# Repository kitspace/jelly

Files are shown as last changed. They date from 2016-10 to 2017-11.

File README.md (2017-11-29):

# Light-following Jellyfish Bristlebot

This is a small light following robot that consists of a simple analog circuit and uses pager vibration motors and toothbrush heads as a form of locomotion. 
This was heavily inspired by [Facelesstech's project](https://facelesstech.wordpress.com/2016/08/15/light-following-bristle-bot/) but adds jellyfishness (with the help of [svg2mod](https://github.com/mtl/svg2mod)).

## Parts
You can buy most of the parts through the [Kitspace page](https://kitspace.org/jelly) but you will also need:

- 2 toothbrush heads (use some old ones!)
- A LiPo battery with a JST connector and built-in protection, anything between 200 - 400mAh should work well (e.g. [from Adafruit](https://www.adafruit.com/product/2750))
- 2 pager vibration motors (e.g. [from Amazon](https://www.amazon.co.uk/Vibration-Motor-TOOGOO-4-6mm-2000RPM/dp/B01H01PXQ2))
- 3 100mm cable ties (e.g. [from Amazon](https://www.amazon.co.uk/Sealey-CT25101-Cable-Ties-100mm/dp/B000RO146I))

## Instructions

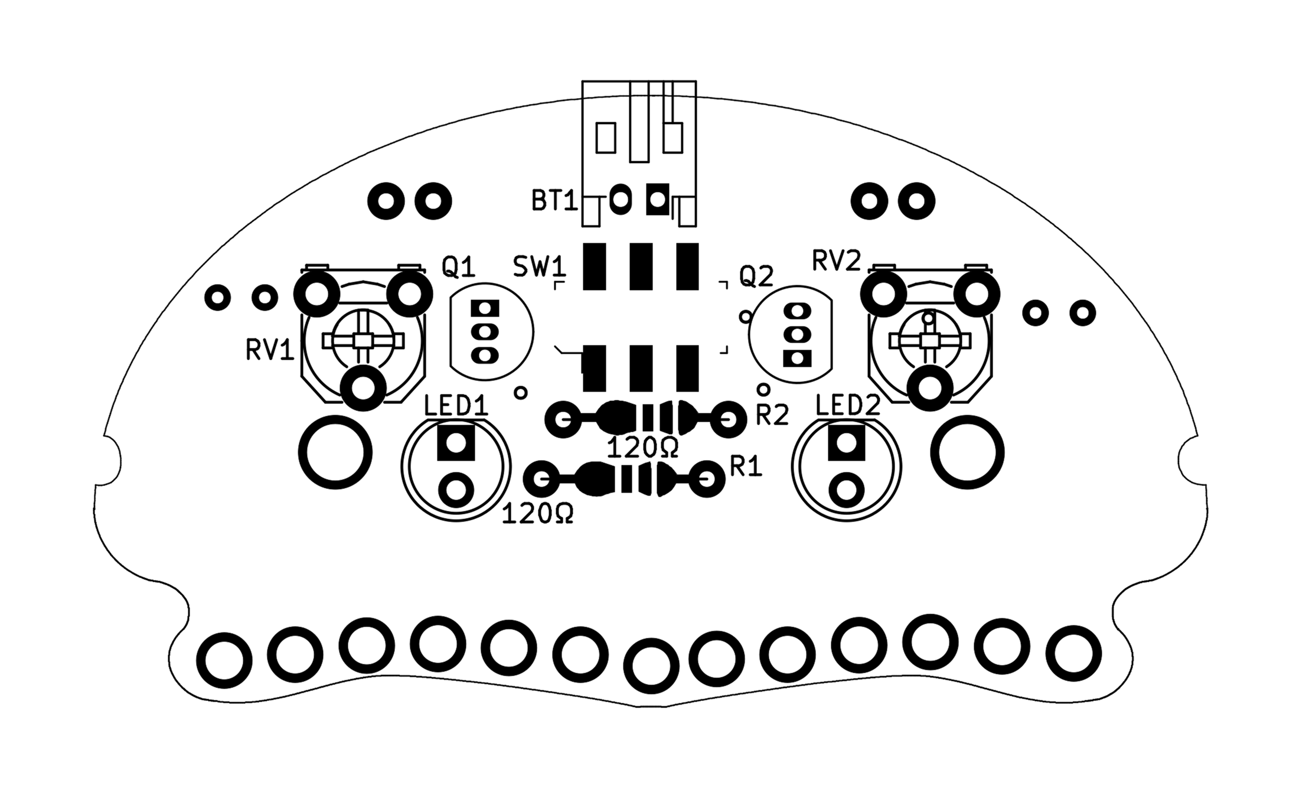
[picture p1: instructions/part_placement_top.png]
top part placement image

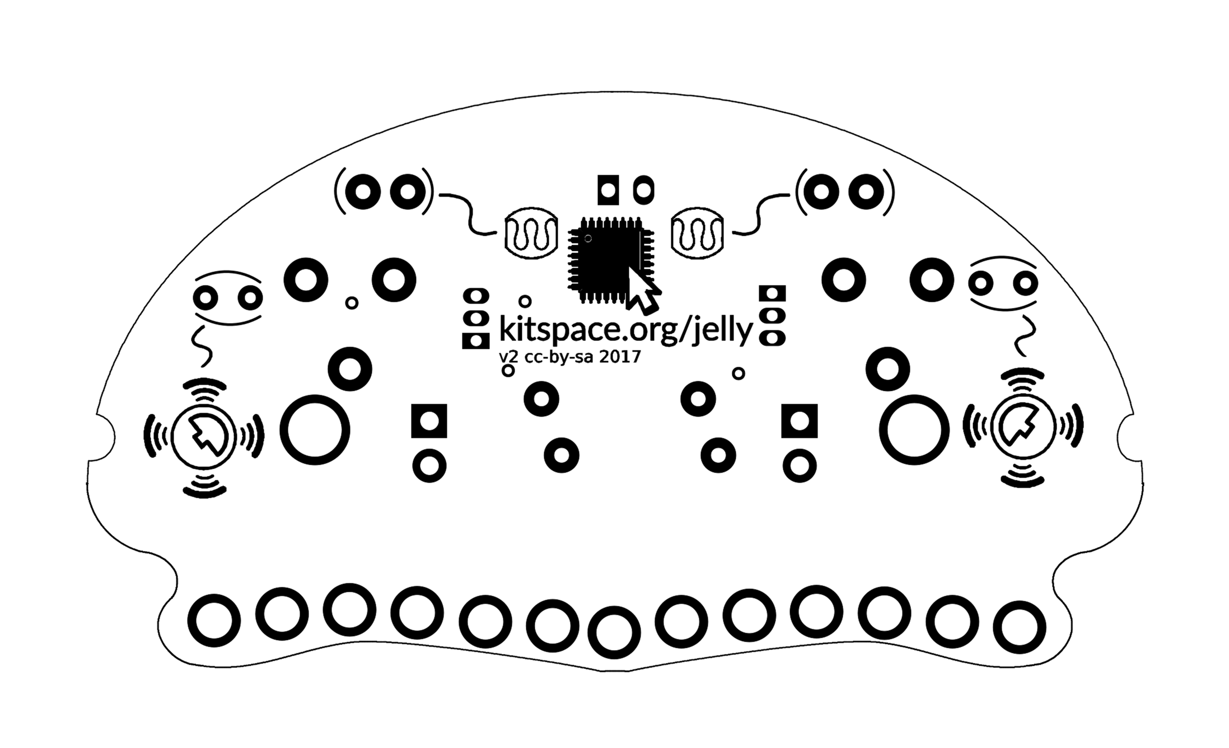
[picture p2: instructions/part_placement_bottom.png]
bottom part placement image


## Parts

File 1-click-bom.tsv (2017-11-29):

References | Qty | Description | Manufacturer | MPN | Digikey | Mouser | RS | Newark | Farnell
BT1 | 1 | Battery connector | JST | S2B-PH-K-S(LF)(SN) | 455-1719-ND |  | 6881353P | 38K8066 | 9491902
LED1, LED2 | 2 | 5MM LED Red | Vishay | TLHK5100 | 751-1118-ND | 78TLHK5100 | 8187580 | 33C1301 | 1328315
PHOTO1, PHOTO2 | 2 | Light dependant resistor |  |  | NSL-19M51-ND |  | 9146710 | 14J5050 | 3168335
Q1, Q2 | 2 | N-Channel MOSFET Tranistor | ON Semiconductor | 2N7000 | 2N7000FS-ND | 5122N7000 | 6714733 | 98K6267 | 9845178
R1, R2 | 2 | Resistor through-hole 1k | TE Connectivity | LR1F1K0 | A105951CT-ND | 594MBB02070C1001FC1 | 148506 | 95W7808 | 2614370
RV1, RV2 | 2 | Trimpot | Bourns | 3306F-1-203 | 3306F-203-ND | 6523306F1203 | 6524316 | 04B2991 | 1689845
SW1 | 1 | SWITCH SLIDE DPDT 300MA 6V | C&K | JS202011SCQN | 401-2002-1-ND | 611JS202011SCQN |  | 95W3256 | 2320019

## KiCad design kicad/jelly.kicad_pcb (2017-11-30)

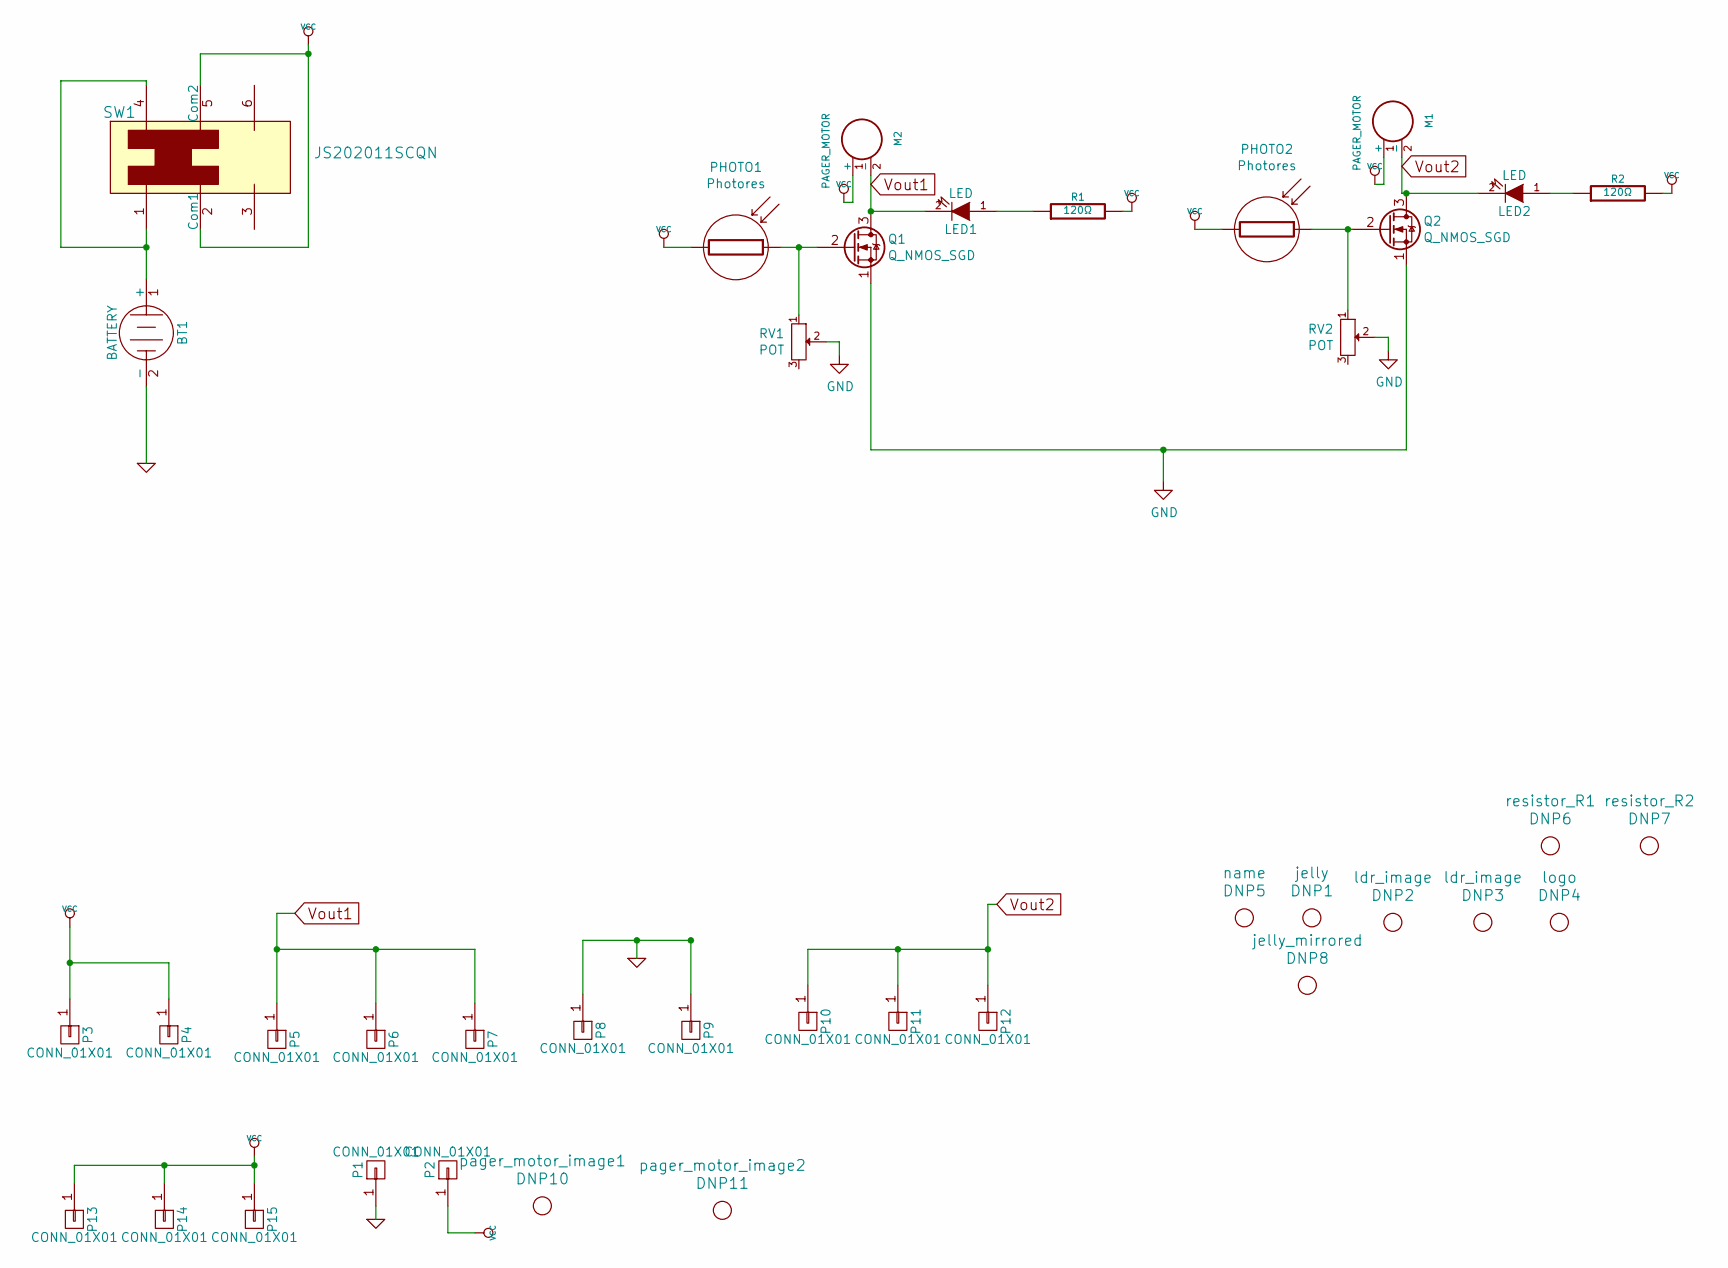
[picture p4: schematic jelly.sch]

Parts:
BT1: BATTERY; JST_PH_S2B-PH-K_02x2.00mm_Angled
DNP1: jelly
DNP2: ldr_image
DNP3: ldr_image; ldr_image_flipped
DNP4: logo
DNP5: name
DNP6: resistor_R1; resistor
DNP7: resistor_R2; resistor
DNP8: jelly_mirrored
DNP10: pager_motor_image1; page_motor_image
DNP11: pager_motor_image2; page_motor_image_flipped
LED1, LED2: LED; LED-5MM; Digikey 751-1118-ND
M1, M2: PAGER_MOTOR; pager_motor_custom
P1, P2: CONN_01X01; hole
P3, P4, P5, P6, P7, P8, P9, P10, P11, P12, P13, P14, P15: CONN_01X01; hole2
PHOTO1, PHOTO2: Photores; ldr; Digikey NSL-19M51-ND
Q1, Q2: Q_NMOS_SGD; TO-92_Inline_Narrow_Oval; Digikey 2N7000FS-ND
R1: 120Ω; R3-5; MPN LR1F1K0; Digikey A105951CT-ND
R2: 120Ω; R3-5; MPN LR1F120R; Digikey S120CACT-ND
RV1, RV2: POT; Potentiometer_Triwood_RM-065; Digikey 3306F-203-ND
SW1: JS202011SCQN; MPN JS202011SCQN; Digi-Key_PN 401-2002-1-ND

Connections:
GND: BT1.2 (-), P1.1, P8.1, P9.1, Q1.1 (S), Q2.1 (S), RV1.2, RV2.2
unnamed: BT1.1 (+), SW1.1, SW1.4
unnamed: LED1.1 (A), R1.1
unnamed: LED2.1 (A), R2.1
unnamed: PHOTO1.1, Q1.2 (G), RV1.1
unnamed: PHOTO2.1, Q2.2 (G), RV2.1
VCC: M1.1 (+), M2.1 (+), P2.1, P3.1, P4.1, P13.1, P14.1, P15.1, PHOTO1.2, PHOTO2.2, R1.2, R2.2, SW1.2 (Com1), SW1.5 (Com2)
Vout1: LED1.2 (K), M2.2 (-), P5.1, P6.1, P7.1, Q1.3 (D)
Vout2: LED2.2 (K), M1.2 (-), P10.1, P11.1, P12.1, Q2.3 (D)

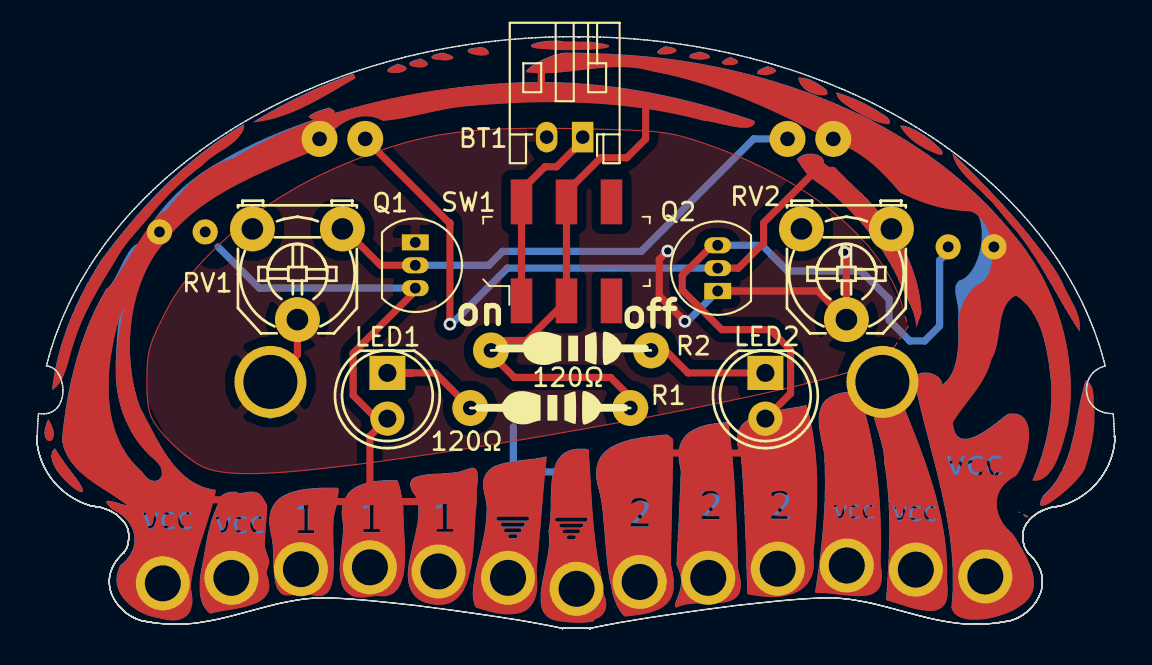
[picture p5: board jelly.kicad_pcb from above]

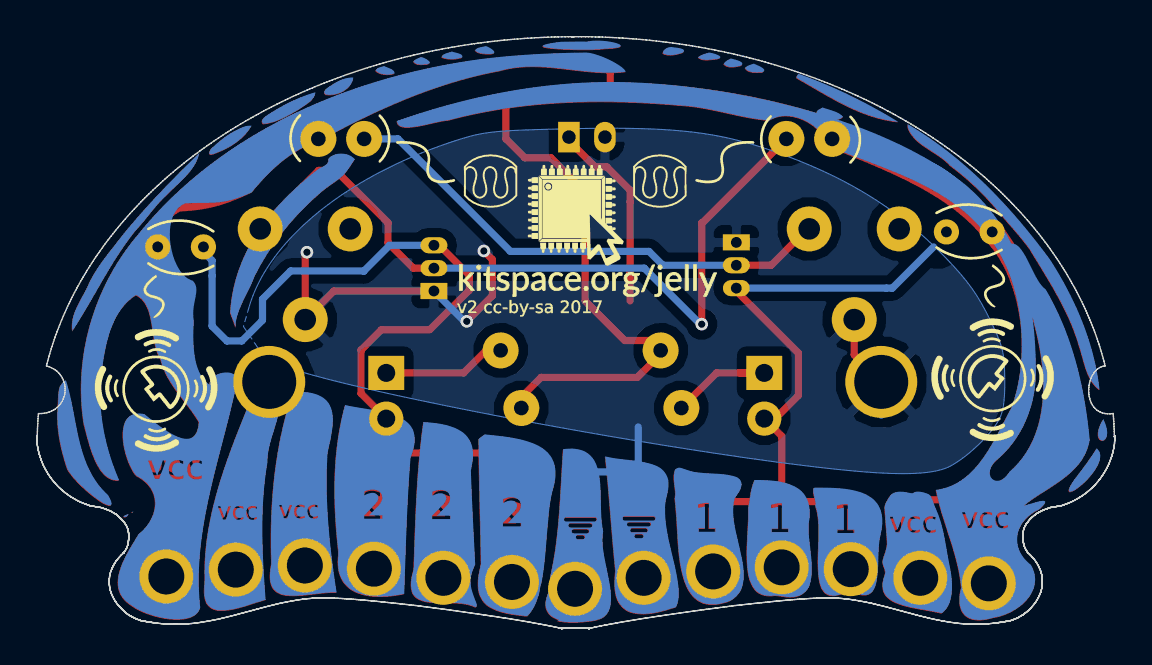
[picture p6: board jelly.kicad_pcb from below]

Board: 2 copper layers, 59.9 x 32.9 mm, 39 parts (5 on the bottom side), 9 nets.

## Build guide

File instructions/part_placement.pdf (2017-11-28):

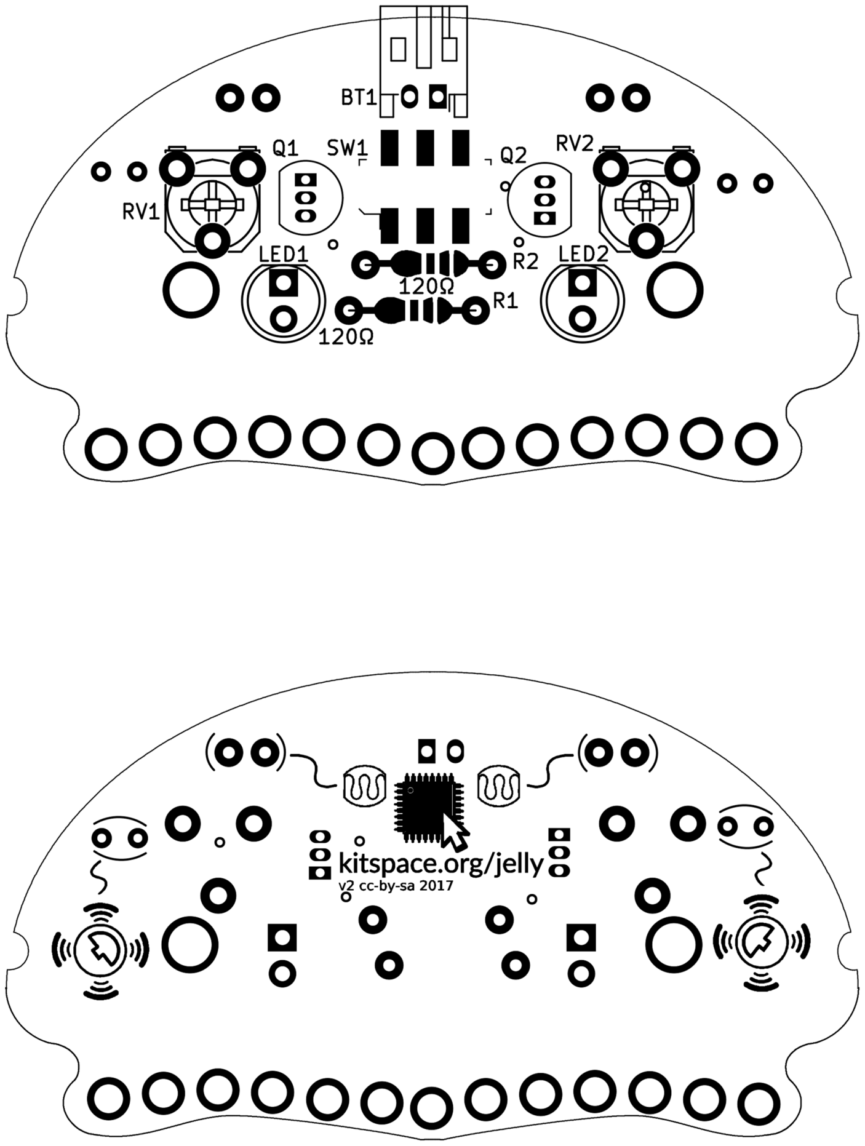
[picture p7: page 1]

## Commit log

2016-08-26 Work on jelly
    [jelly.kicad_pcb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]
2016-08-26 Work on jelly copper
    [jelly-B.Cu.gbr, jelly-B.Mask.gbr, jelly-B.SilkS.gbr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]
2016-08-26 Adjust copper on jelly
    [jelly.kicad_pcb]
2016-08-27 Add some components
    [jelly.sch]
2016-08-27 Add kitnic.yaml and 1-click-bom
    [1-click-bom.tsv]
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2016-08-27 Remove holes from jelly pads
    [jelly.kicad_pcb]
2016-08-27 Plot Gerbers
    [jelly-B.Cu.gbr, jelly-B.Mask.gbr, jelly-B.SilkS.gbr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]
2016-08-27 Play with layout
    [jelly.kicad_pcb, jelly.sch]
2016-08-28 Layout some components
    [jelly-B.Cu.gbr, jelly-B.Mask.gbr, jelly-B.SilkS.gbr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]
2016-08-28 Move things about
    [jelly.kicad_pcb, jelly.sch]
2016-08-28 Re-plot gerbers
    [jelly-B.Cu.gbr, jelly-B.Mask.gbr, jelly-B.SilkS.gbr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]
2016-08-28 Add LDR silkscreen image
    [jelly.kicad_pcb, jelly.sch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]
2016-08-28 Re-arrange connector holes
    [jelly-B.Cu.gbr, jelly-B.Mask.gbr, jelly-B.SilkS.gbr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]
2016-08-28 Add notches to outline and remove holes
    [jelly-B.Cu.gbr, jelly-B.Mask.gbr, jelly-B.SilkS.gbr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]
2016-08-28 Adjust copper specks near edges
    [jelly-B.Cu.gbr, jelly-B.Mask.gbr, jelly-B.SilkS.gbr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]
2016-08-28 Make room for motor pads
    [jelly-B.Cu.gbr, jelly-B.Mask.gbr, jelly-B.SilkS.gbr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]
2016-08-28 Adjust position of right motor
    [jelly-B.Cu.gbr, jelly-B.Mask.gbr, jelly-B.SilkS.gbr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]
2016-08-28 Play around with some routing
    [jelly-B.Cu.gbr, jelly-B.Mask.gbr, jelly-B.SilkS.gbr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]
2016-08-28 Switch to CR2450 battery holder
    [1-click-bom.tsv, jelly.kicad_pcb, jelly.sch]
2016-08-28 Try and fit things in around CR2450
    doesn't look possible
    [jelly.kicad_pcb]
2016-08-28 Give up on CR2450
    [jelly.kicad_pcb, jelly.sch]
2016-09-28 Turn of visibility of footprint fields in schematic
    [jelly.kicad_pcb, jelly.sch]
2016-09-28 Add tilt switch and work out transistor choice
    [jelly.sch]
2016-09-28 Switch to low side switch and layout about
    [jelly.kicad_pcb, jelly.sch]
2016-10-08 Make jelly get out of the way
    [jelly.kicad_pcb]
2016-10-08 Work on silkscreen and jelly
    [jelly.kicad_pcb]
2016-10-08 Adjust traces and plot
    [jelly-B.Cu.gbr, jelly-B.Mask.gbr, jelly-B.SilkS.gbr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]
2016-10-08 Remove values from plot
    [jelly-B.Cu.gbr, jelly-B.Mask.gbr, jelly-B.SilkS.gbr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]
2016-10-08 Draw names on pads
    [jelly-B.Cu.gbr, jelly-B.Mask.gbr, jelly-B.SilkS.gbr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]
2016-10-08 Work on pad names
    [jelly-B.Cu.gbr, jelly-B.Mask.gbr, jelly-B.SilkS.gbr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]
2016-10-15 Work on jelly pad labels
    [jelly-B.Cu.gbr, jelly-B.Mask.gbr, jelly-B.SilkS.gbr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]
2016-10-15 Add logo and name
    [jelly.kicad_pcb, jelly.sch]
2016-10-15 Use triangle labels
    [jelly.kicad_pcb]
2016-10-15 Move labels down
    [jelly-B.Cu.gbr, jelly-B.Mask.gbr, jelly-B.SilkS.gbr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]
2016-10-15 Make image for LDR silkscreen
    [jelly.kicad_pcb, jelly.sch]
2016-10-15 Add resistor silkscreen
    [jelly-B.Cu.gbr, jelly-B.Mask.gbr, jelly-B.SilkS.gbr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]
2016-10-15 Fix some traces
    [jelly-B.Cu.gbr, jelly-B.Mask.gbr, jelly-B.SilkS.gbr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]
2016-10-15 Rename leds from D to LED
    [jelly.kicad_pcb, jelly.sch]
2016-10-15 Add page motor silkscreen image
    [jelly.kicad_pcb, jelly.sch]
2016-10-15 Adjust LDR silkscreen brackets
    [jelly.kicad_pcb]
2016-10-15 Add plus and minus labels
    [jelly.kicad_pcb, jelly.sch]
2016-10-15 Move LDR drawings
    [jelly.kicad_pcb]
2016-10-15 Move Q references
    [jelly.kicad_pcb]
2016-10-16 Add mercury switch drawing
    [jelly-B.Cu.gbr, jelly-B.Mask.gbr, jelly-B.SilkS.gbr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]
2016-10-16 Move jelly slightly out of the way
    [jelly.kicad_pcb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]
2016-10-16 Make sure footprints and schematic are in sync
    [jelly.kicad_pcb, jelly.sch]
2016-10-16 Adjust triangle labels
    [jelly-B.Cu.gbr, jelly-B.Mask.gbr, jelly-B.SilkS.gbr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]
2016-10-16 Remove fills
    [jelly.kicad_pcb]
2016-10-16 Use svg2mod to get a polygon for zone
    [jelly.kicad_pcb]
2016-10-16 Adjust logo size
    [jelly.kicad_pcb]
2016-10-16 Run DRC and plot
    [jelly-B.Cu.gbr, jelly-B.Mask.gbr, jelly-B.SilkS.gbr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]
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2016-10-16 Add creative commons logo
    [jelly-B.Cu.gbr, jelly-B.Mask.gbr, jelly-B.SilkS.gbr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]
2016-10-16 Add copper zone cutout around cc logo
    [jelly-B.Cu.gbr, jelly-B.Mask.gbr, jelly-B.SilkS.gbr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]
2016-10-16 Clear old values in BOM
    [1-click-bom.tsv]
2017-03-05 Make sure pcb can be opened in kicad stable
    [jelly.kicad_pcb]
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2017-03-05 Fix resistor selection and improve BOM
    [1-click-bom.tsv]
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2017-05-25 Increase annular rings on quite a few pads
    fixes #2
    [jelly.kicad_pcb, jelly.sch]
2017-05-25 Switch to stable kicad and re-plot
    [jelly-B.Cu.gbr, jelly-B.Mask.gbr, jelly-B.SilkS.gbr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]
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2017-11-28 Add new switch and battery connector
    [jelly.kicad_pcb, jelly.sch]
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2017-11-28 Update jelly svg and netlist
    [jelly.kicad_pcb, jelly.sch]
2017-11-28 Add jelly drawing on the back
    [jelly.kicad_pcb, jelly.sch]
2017-11-28 Adjust jelly for pad
    [jelly.kicad_pcb]
2017-11-28 Mirror jelly pad names
    [jelly-B.Cu.gbr, jelly-B.Mask.gbr, jelly-B.SilkS.gbr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]
2017-11-28 Adjust silkscreen and plot
    [jelly-B.Cu.gbr, jelly-B.Mask.gbr, jelly-B.SilkS.gbr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]
2017-11-28 Adjust silkscreen and start on instructions
    [jelly-B.Cu.gbr, jelly-B.Mask.gbr, jelly-B.SilkS.gbr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]
2017-11-28 Add on/off to silkscreen near switch
    [jelly-B.Cu.gbr, jelly-B.Mask.gbr, jelly-B.SilkS.gbr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]
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2017-11-30 Fix motor connections
    [jelly-B.Cu.gbr, jelly-B.Mask.gbr, jelly-B.SilkS.gbr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]
